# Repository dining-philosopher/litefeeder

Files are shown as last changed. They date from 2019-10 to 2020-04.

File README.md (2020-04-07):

# litefeeder

Semi-automatic passive printable/castable SMD tape feeder for LitePlacer (should work with other pick and place machines with some adjustments).

Watch it in action: https://www.youtube.com/watch?v=S1jxeCK4YC0

Discussion: https://liteplacer.com/phpBB/viewtopic.php?f=11&t=6272 https://groups.google.com/forum/#!topic/openpnp/D-vYZLsAWHc

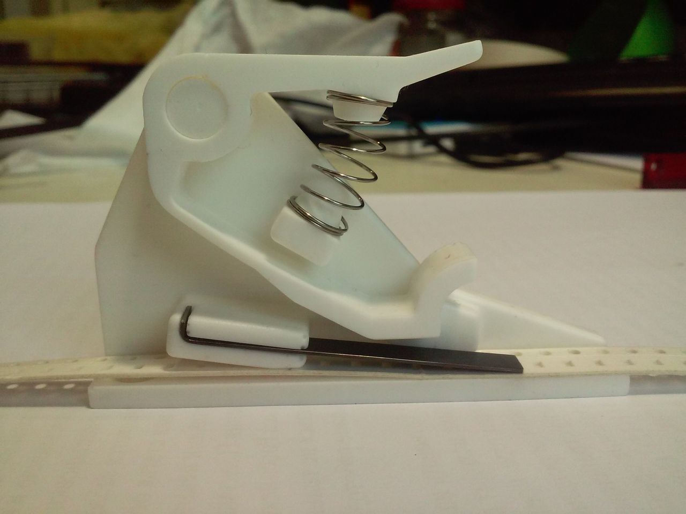
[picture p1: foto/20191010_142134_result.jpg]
assembled feeder


## Update

Jed Smith made film peeler for it, so now it is fully automatic! https://groups.google.com/d/msg/openpnp/D-vYZLsAWHc/gkkAq5XVAgAJ https://loonatec.com/pnp-semi-automatic-feeder/ https://bitbucket.org/Loonatec/pnp_semi-automatic_feeder/ So please use that design until i update this page.

## General notes

The design is inspired by alexavr2's alexfeeder https://github.com/alexavr2/alexfeeder https://alex-avr2.livejournal.com/210450.html and Karl Ekdahl's clockwork feeder https://liteplacer.com/phpBB/viewtopic.php?f=11&t=191 https://vimeo.com/144454867 http://www.knasmusic.com/diyeverything/pickandplace/tapefeeders.php . It is easy to manufacture as the former and requires no additional motion as the latter.

However i think the best cheap feeder design is that found in chinese machines. https://youtu.be/GKw8WOlGR84?t=131 https://youtu.be/y14pdfjYsyo But it requires software support, ~~also i did not find the tape pulling rod assembly sold separately in chinese stores,~~ and i think it should be problematic to attach such assembly to an existing machine. UPD: Here they are: https://www.robotdigg.com/product/1641/Charmhigh-Pull-Pin-Blue-Magnet-Spring-Set-for-36VA-48VA-48VB https://www.robotdigg.com/product/561/Desktop-PnP-Mat https://www.robotdigg.com/product/560/Desktop-PnP-Tape-and-Reel-Receiving-Wheel

### Pros

* No software support required.
* No extra machine head movement required.
* No extra electronics required.
* Easy to manufacture.
* Low cost (about $1 per feeder without labor).

### Cons

* Can only feed 8/4 mm (and maybe 12/4 mm) tape.
* Does not peel the film. You can use 150 - 200 g weights for this or make film peeler as in chinese machines or alexfeeder.

## Manufacturing

### Parts needed

* 0.5*5 mm flat spring. https://www.aliexpress.com/item/32826247091.html
* 0.5\*8\*25 mm coil spring (20 mm may be fine too). https://www.aliexpress.com/item/33054199528.html
* 1.2 mm round nylon line for the tooth (1 mm may be fine too, also you can use metal pins from headers, but it requires additional filing).
* Super glue.
* 7*11 mm nylon spacers for the axle (optional, not needed if you print directly). https://www.aliexpress.com/item/32868508973.html
* Two 2.5*20 mm wood screws.
* One M3*35 screw for machine head.
* One plastic cap for machine head. I use M3 acorn nut https://www.aliexpress.com/item/32963279606.html , but you can use (rounded) M3 long nylon nut https://www.aliexpress.com/item/33002921745.html for better height adjustment or print your own cap.

### [Printing and casting](casting.md)

You can make it with your favorite technology, but if you have no 3d printer at all, or your prints are not strong enough, and/or you prefer casting over 3d printing, you may want to read my [casting description](casting.md).

### Assembly

Drill 1.2 mm hole at about 45° at the end of the dog.
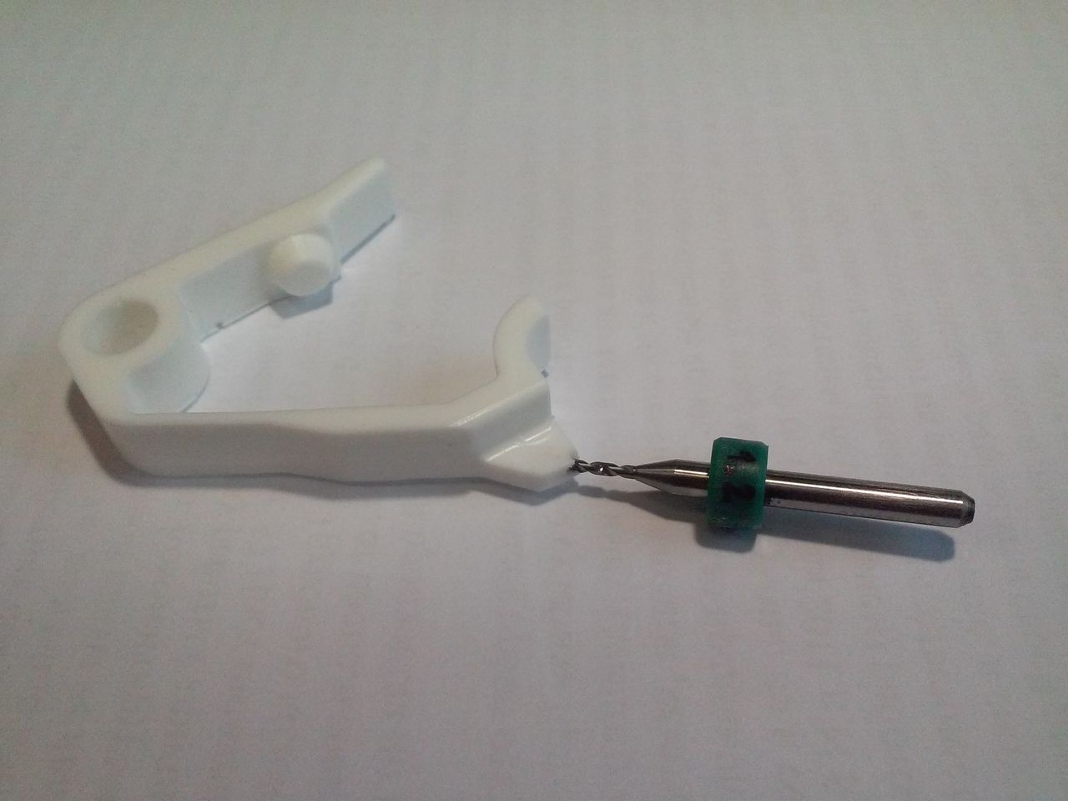
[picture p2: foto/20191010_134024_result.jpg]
drilling tooth hole


Glue 1.2 mm nylon line into this hole.
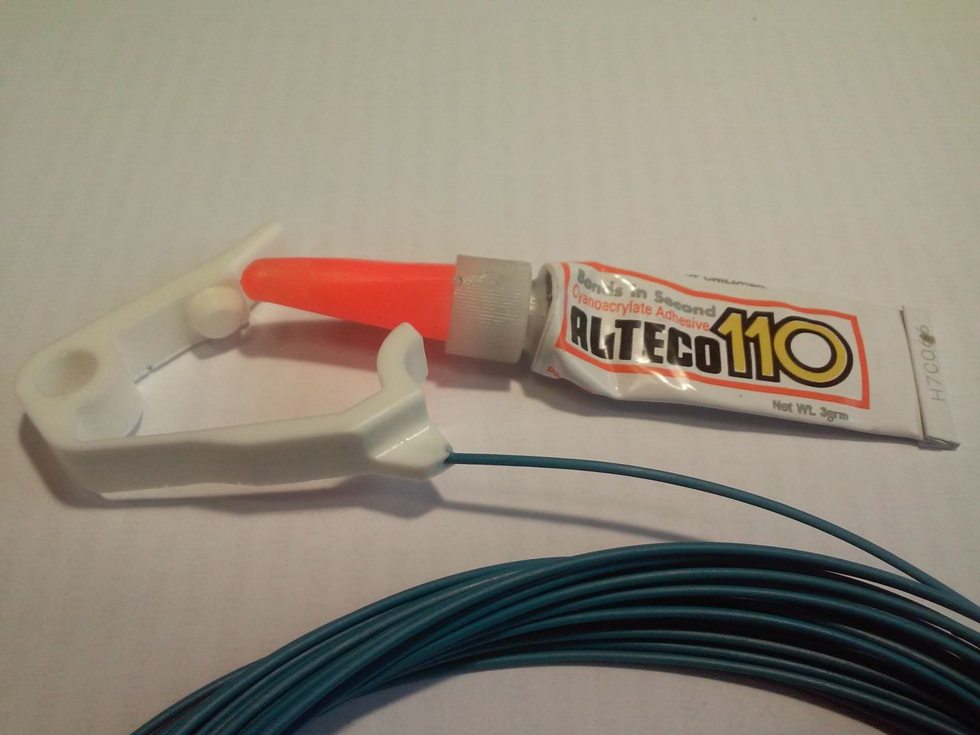
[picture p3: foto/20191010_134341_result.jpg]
gluing nylon tooth

<!---![](foto/20191010_135132_result.jpg "cutting the tooth")-->

Cut the line flush to the vertical face. So we have durable nylon tooth that will push the tape by its holes. You can also use metal pins, nails or whatever you want, but i think nylon line is the easiest way.
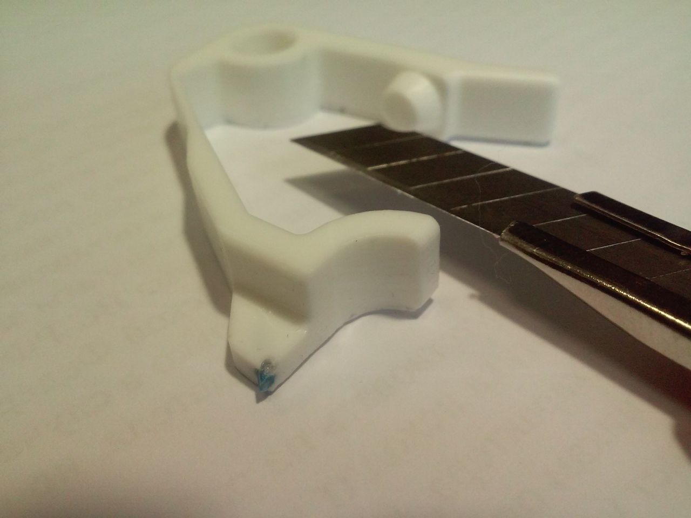
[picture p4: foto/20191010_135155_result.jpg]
cutting the tooth


Bend and cut the flat spring so its long side is 43 - 44 mm and short side is 2 - 3 mm.
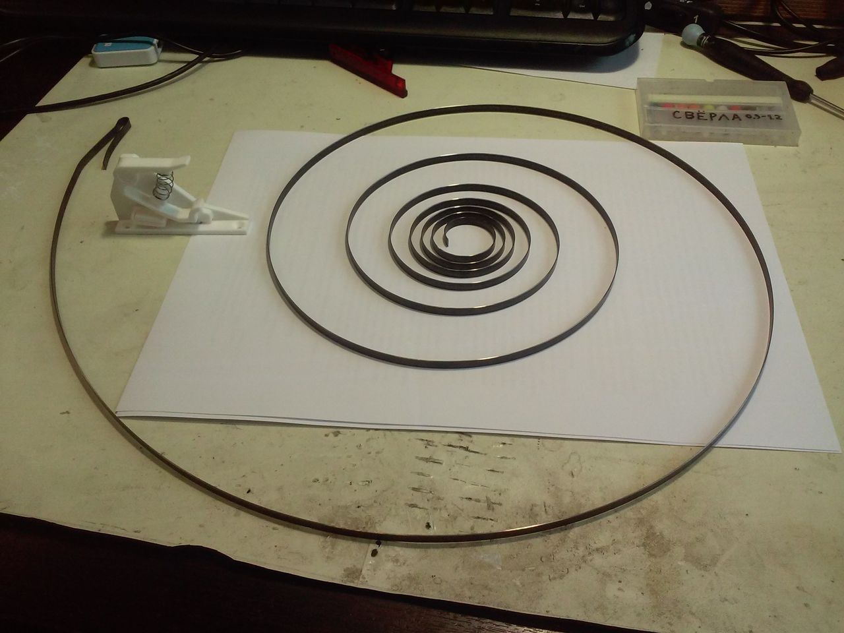
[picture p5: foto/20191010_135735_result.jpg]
flat spring source

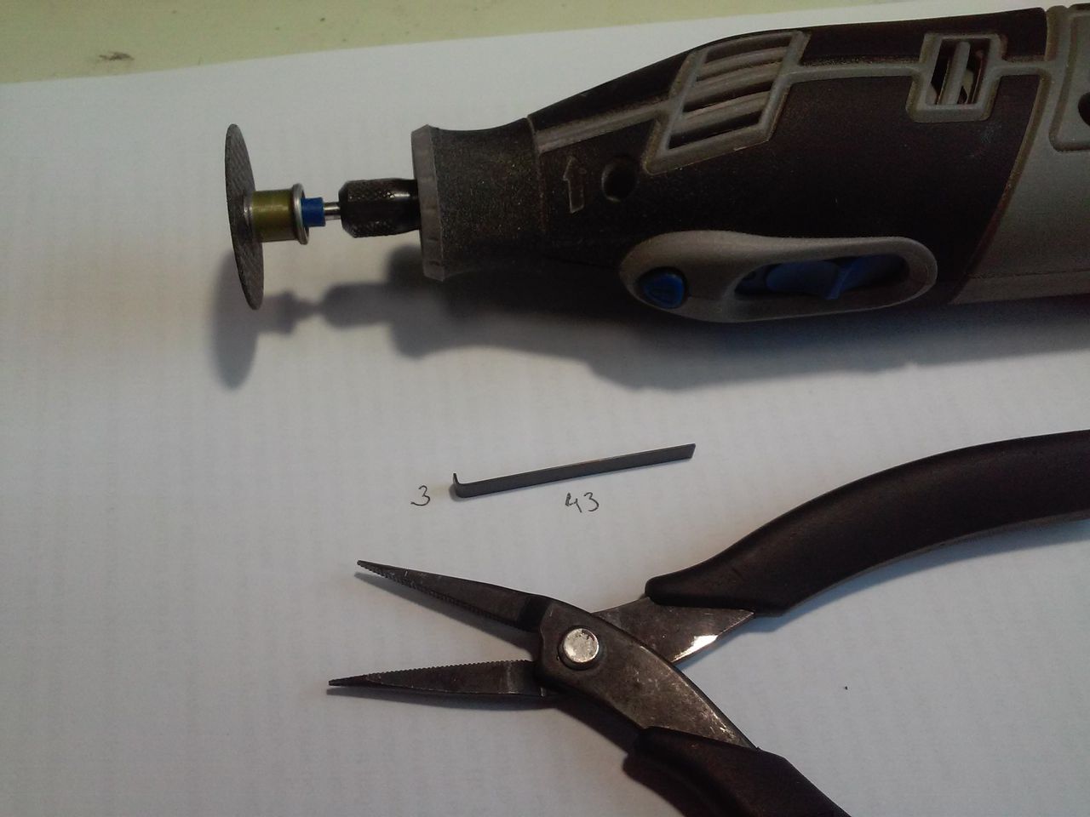
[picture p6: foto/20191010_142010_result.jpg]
cutting flat spring

<!---![](foto/20191010_142122_result.jpg "assembled feeder")-->

Assemble the feeder.
assembled feeder
<!---![](foto/20191010_142910_result.jpg "silicone mold with nylon axle inserted")-->
<!---![](foto/20191010_155337_result.jpg "template aligned to the liteplacer")-->

Replace one of the screws that hold the lower linear bearing with the 35 mm screw and attach the cap nut so your machine can push the lever.
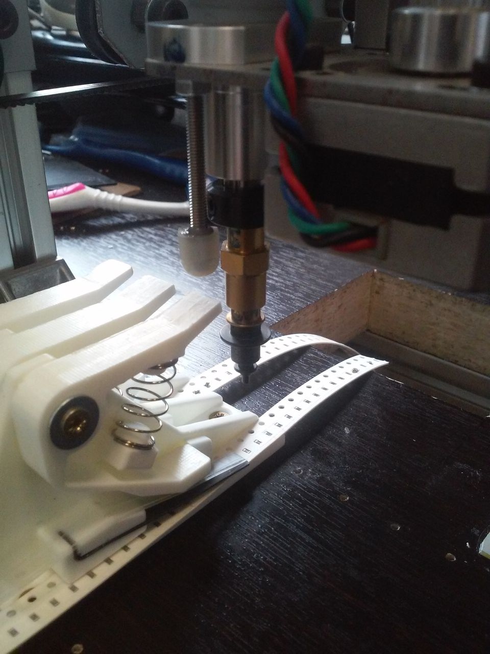
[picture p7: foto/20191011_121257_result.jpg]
feeders in place feeders in place 4


It's time to ruin the table where the machine rests. But before this you need to determine the right Y position for your feeders. Insert some tape into the feeder and push the lever several times. Now you know that it works (hopefully) and the machine nozzle should be above the first part cell not covered by the spring. Try to find such Y position that your feeder pickup coordinate will be almost at the lowest allowed Y coordinate (it is -3 mm in case of the liteplacer, so aim to about -2 mm).
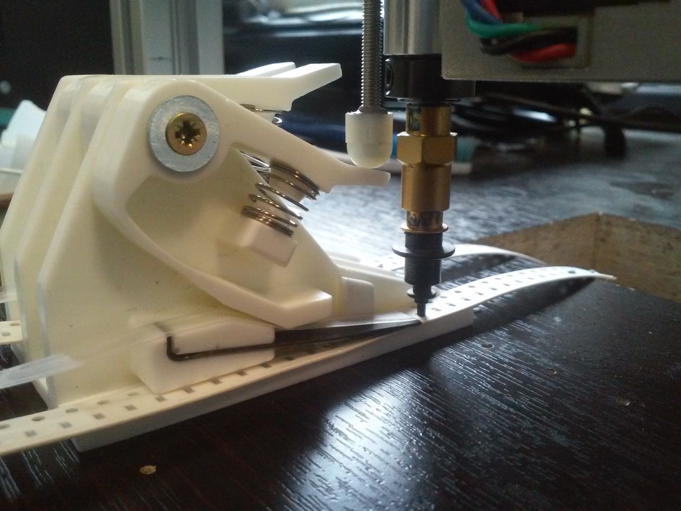
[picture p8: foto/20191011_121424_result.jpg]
feeder in action feeder in action 1

<!---![feeder in action](foto/20191011_121431_result.jpg "feeder in action 2")-->

Print the feeder_screw_template.pdf and stick it to the table (ideally, but not necessary, parallel to the X axis). So your feeders will sit on the table with exactly 12 mm pitch. 
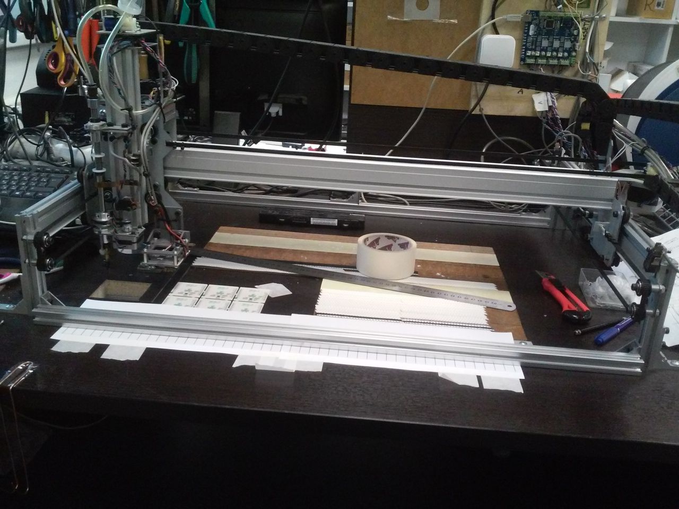
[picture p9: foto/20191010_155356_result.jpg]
template aligned to the liteplacer


Punch holes at the line crossings.
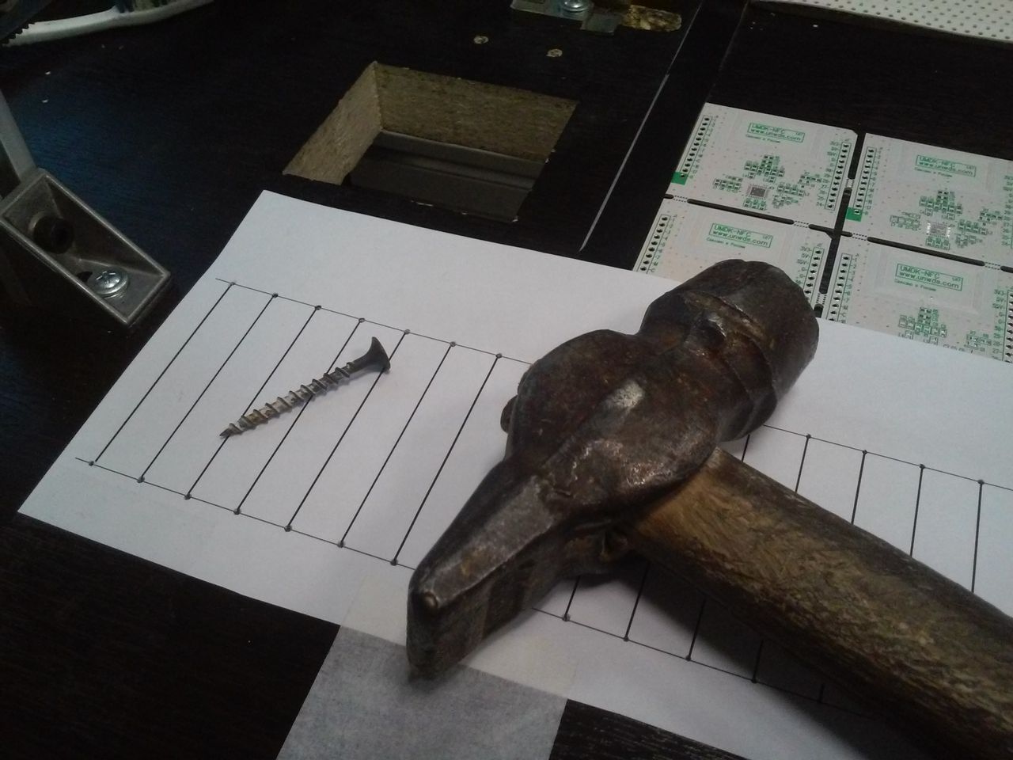
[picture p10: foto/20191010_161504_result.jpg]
punching center holes for the feeders according to the template


Drill 1.5 mm holes.
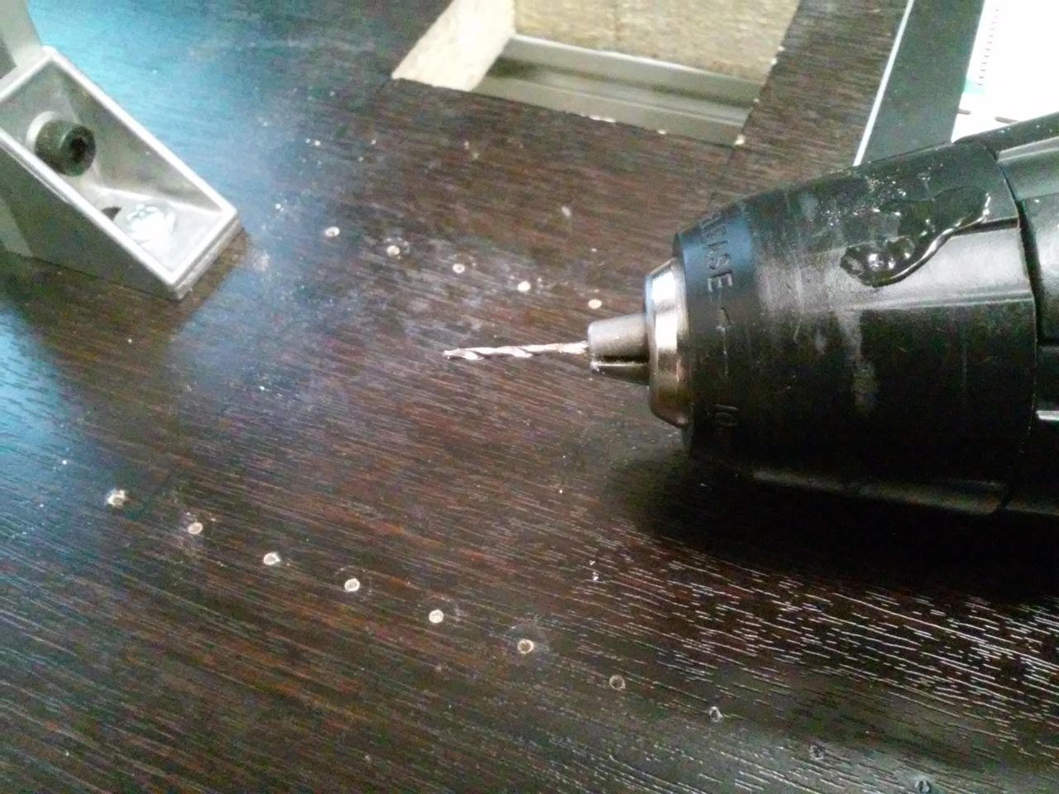
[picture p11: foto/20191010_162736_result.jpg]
drilling holes for the feeders

<!---![feeders in place](foto/20191010_170919_result.jpg "feeders in place 1")-->

Drill 45° 8.5 - 10 mm hole for each feeder into which the used tape will be discarded (not pictured yet). At the first time you may use existing camera hole (the camera is anyway useless with the existing liteplacer software).

Screw some feeders.
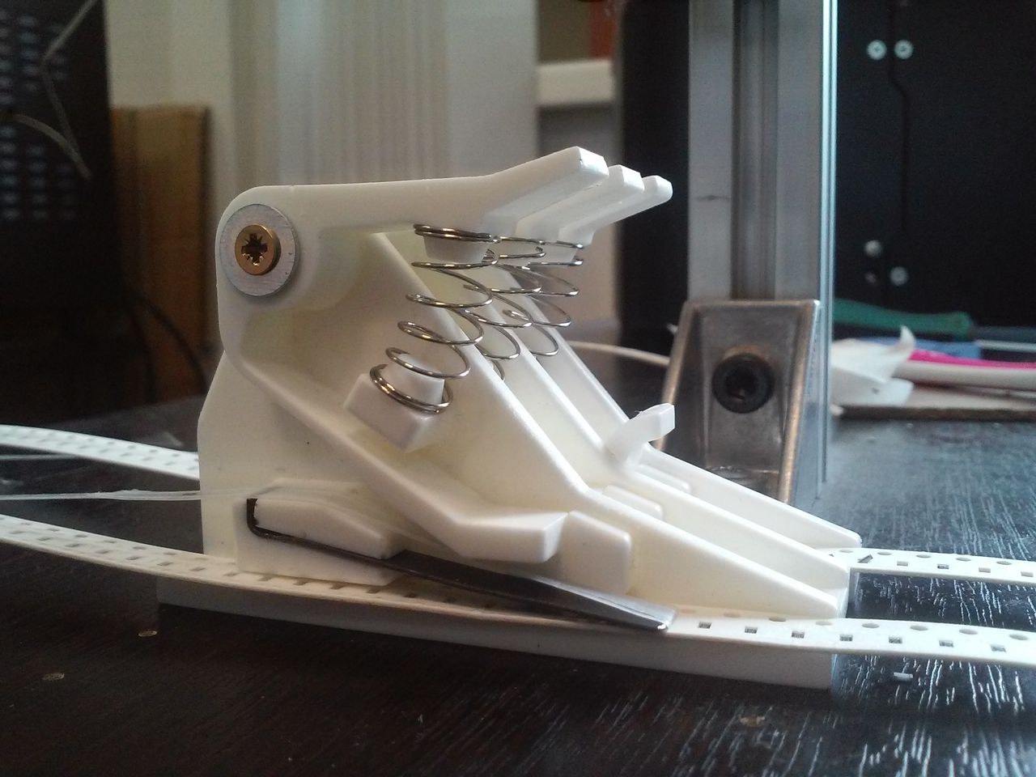
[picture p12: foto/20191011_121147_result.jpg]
feeders in place feeders in place 2

<!---![feeders in place](foto/20191011_121207_result.jpg "feeders in place 3")-->

Invent some reel mount and film peeling mechanism.
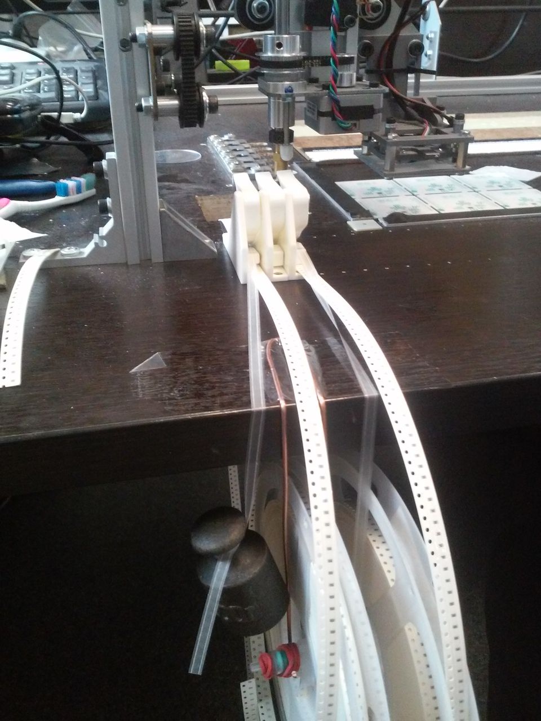
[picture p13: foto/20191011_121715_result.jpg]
reel mount and film peeling mechanism


Profit!

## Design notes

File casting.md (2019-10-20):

# Printing and casting the litefeeder

You can make it with your favorite technology, but bear in mind that it contains plastic spring and rubbing parts, so the plastic should be strong and durable to some extent. For example, UV photopolymers for LCD printers (at least that i have) do not meet this requirements (and also my printer prints quite slowly), so i had to cast my feeders from polyurethane (Smooth-Cast 305).

There are number of polyurethane casting tutorials on youtube, e. g. https://www.youtube.com/watch?v=YGZ2OeQinzw https://www.youtube.com/watch?v=DEVi0mEaJJQ

Platinum silicones are generally better, but they are incompatible with most photopolymers with notable exception of Gorky Liquid Simple https://gorkyliquid.ru/catalog/fotopolimer-dlya-3d-printera/fotopolimernaya_smola_gorky_liquid_simple_krasnaya_1_kg which is quite good by other parameters and also is the cheapest photopolymer in my country. If you can not purchase this resin, try finding another platinum silicone compatible photopolymer or use tin silicone. "Protective coatings" do not work, at least to me.

Release agent is mandatory, especially when pouring second half of the silicone mold over the first half. I use Ease-Release 200. When casting polyurethane, applying release agent before each casting is not necessary, but it is good to apply it every 2 - 3 castings.

Each mold lasts for about 10 - 20 castings (30 if you are lucky, but it slightly grows with each casting).

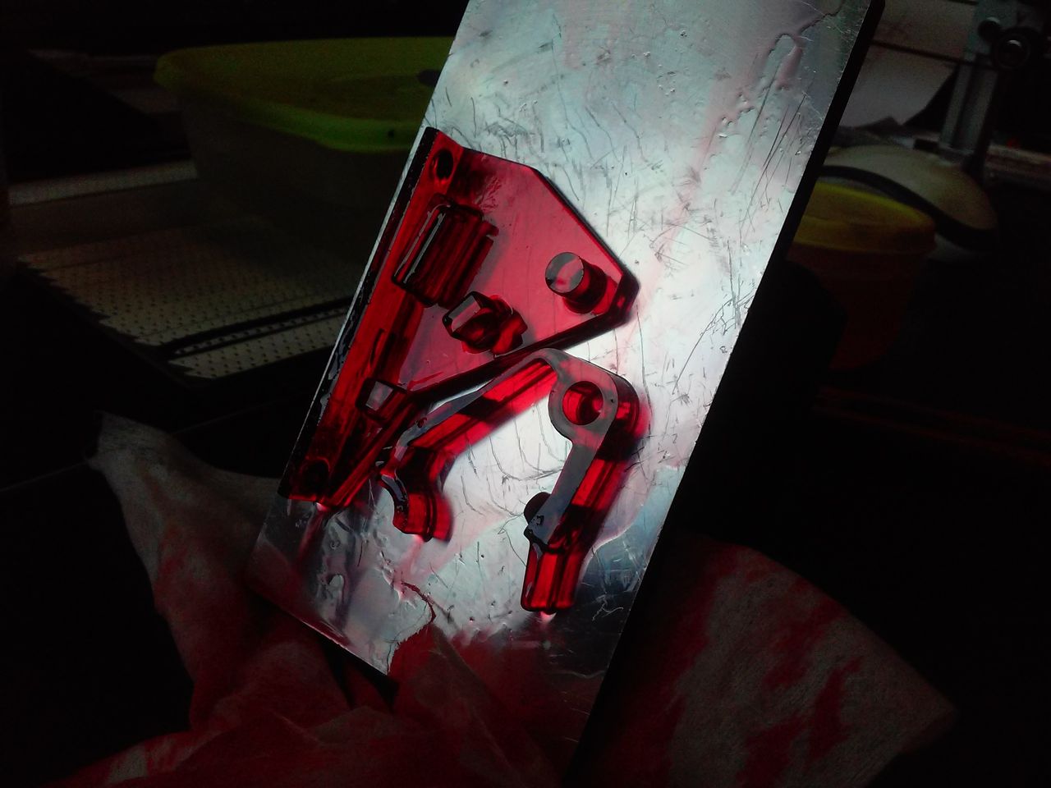
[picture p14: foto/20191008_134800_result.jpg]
printed feeder on the substrate

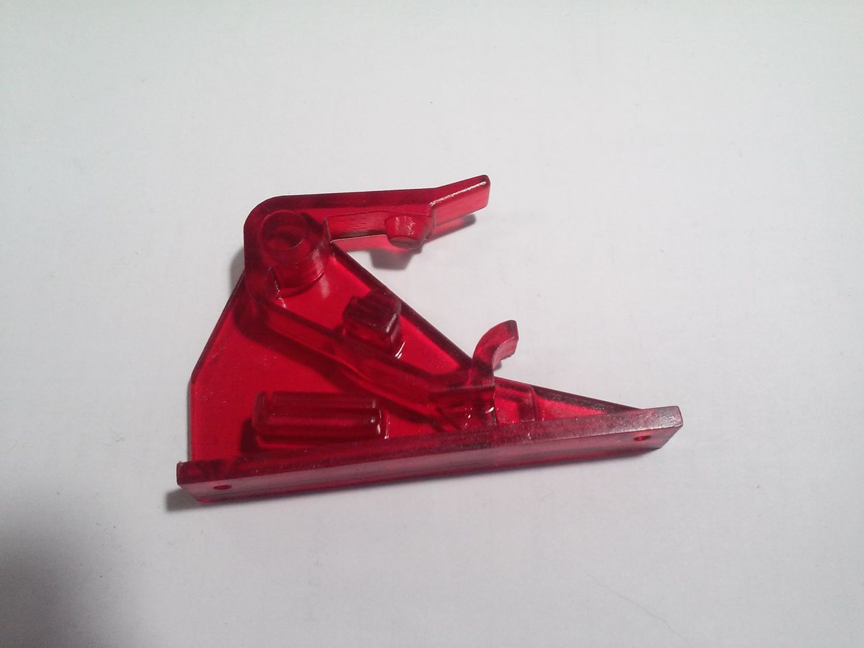
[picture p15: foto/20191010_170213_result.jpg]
printed and washed feeder


Sculpt some keys from modeling clay and glue the feeder parts with the same clay. It is said that some clays are incompatible with platinum silicones, but all my clays work fine.
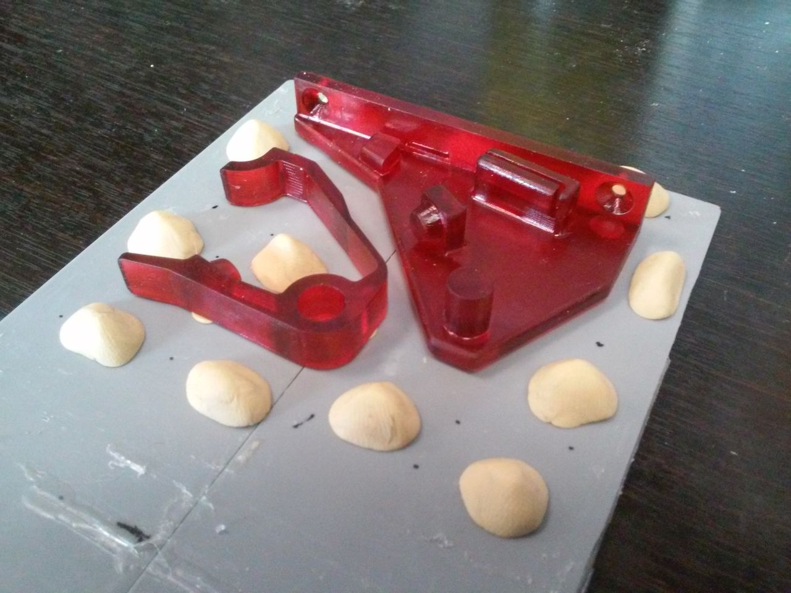
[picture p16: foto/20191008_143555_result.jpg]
preparing for first half silicone molding

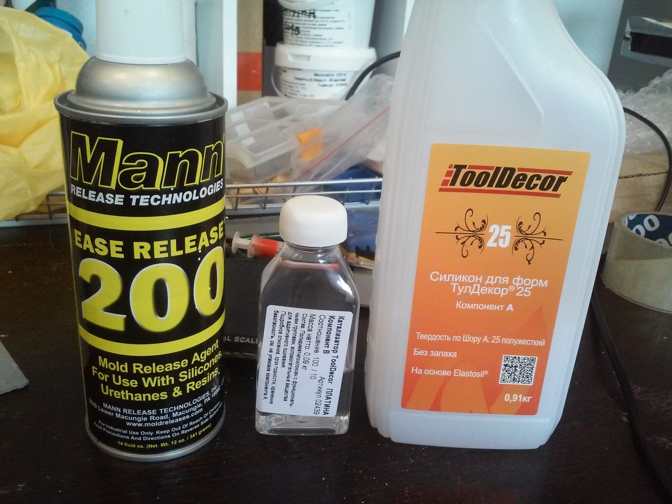
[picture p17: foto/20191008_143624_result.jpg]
silicone and release agent

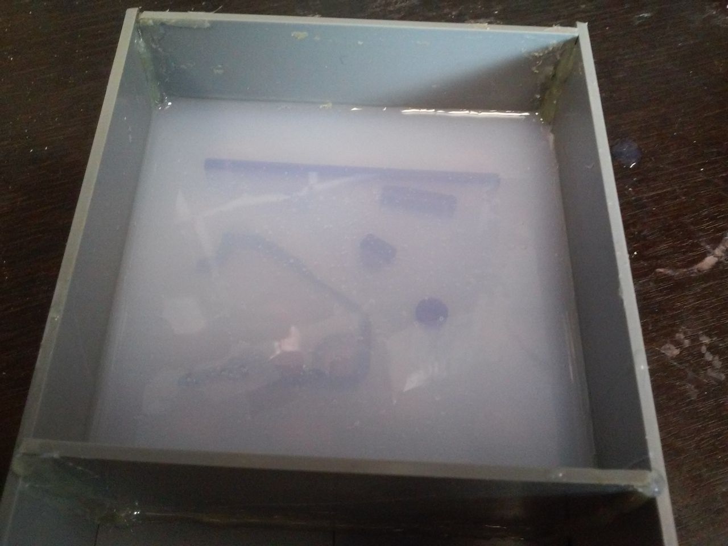
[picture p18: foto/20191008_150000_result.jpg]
first half silicone curing


Remove excess silicone.
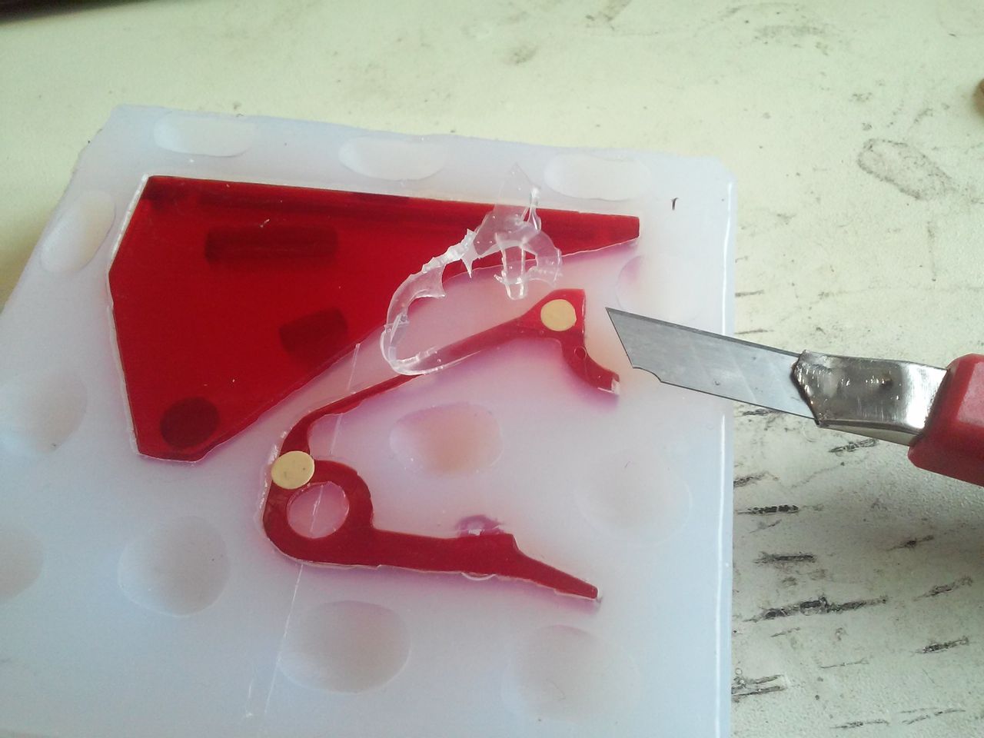
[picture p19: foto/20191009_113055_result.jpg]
removing excess silicone

<!---![](foto/20191009_121346_result.jpg "scotch bucket for second half of the silicone mold")-->

Quick and dirty vessel for the second half. Apply release agent! And do not forget spouts and vents.
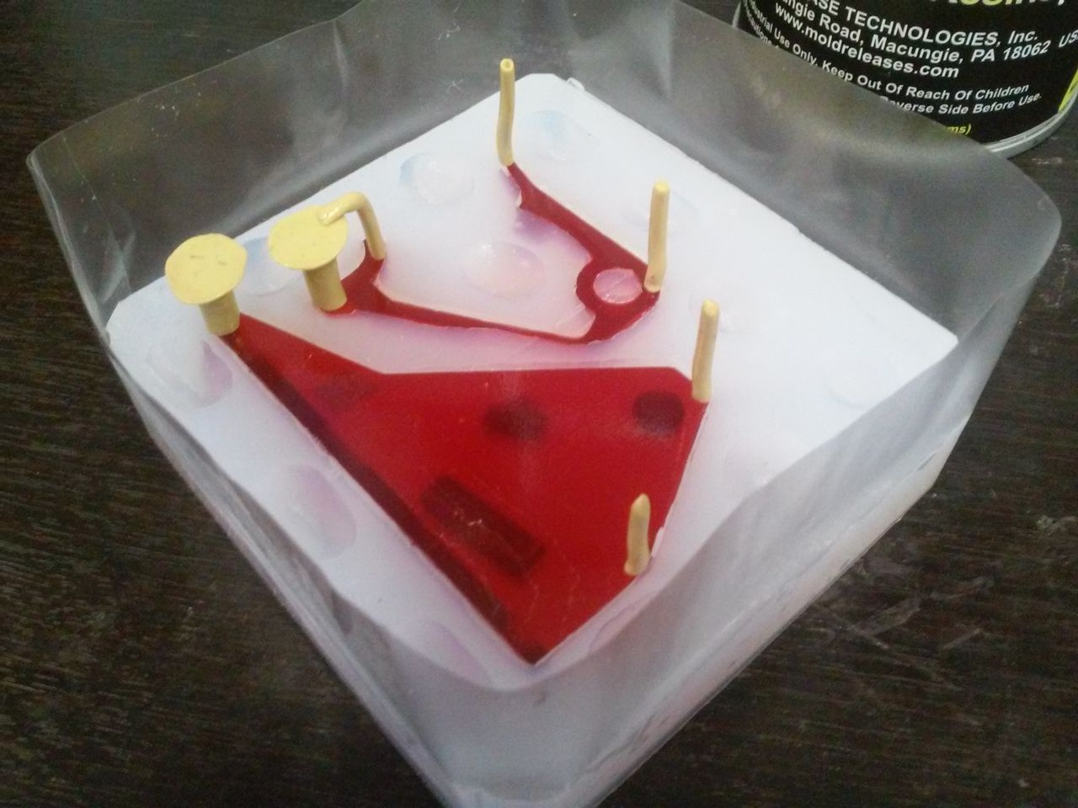
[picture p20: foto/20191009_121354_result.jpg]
scotch bucket for second half of the silicone mold

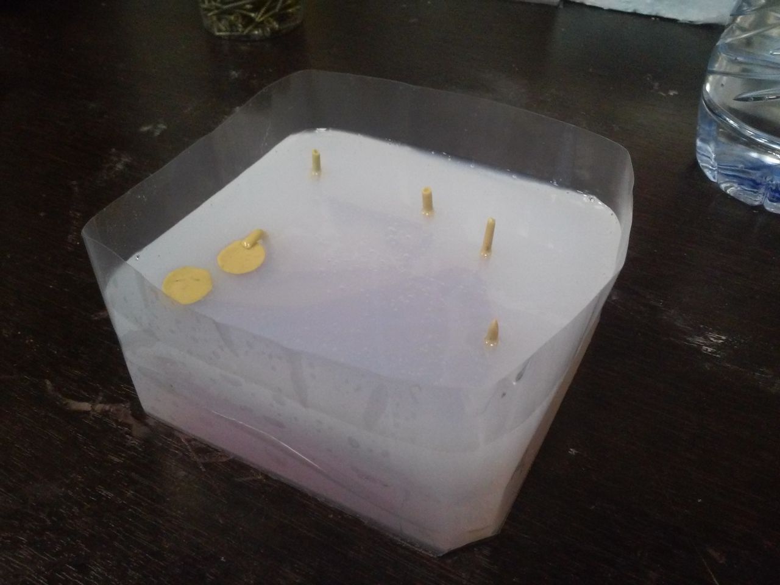
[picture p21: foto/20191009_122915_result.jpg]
scotch bucket for second half of the silicone mold second half silicone curing


Insert nylon axle if you have them (but it also works without it).
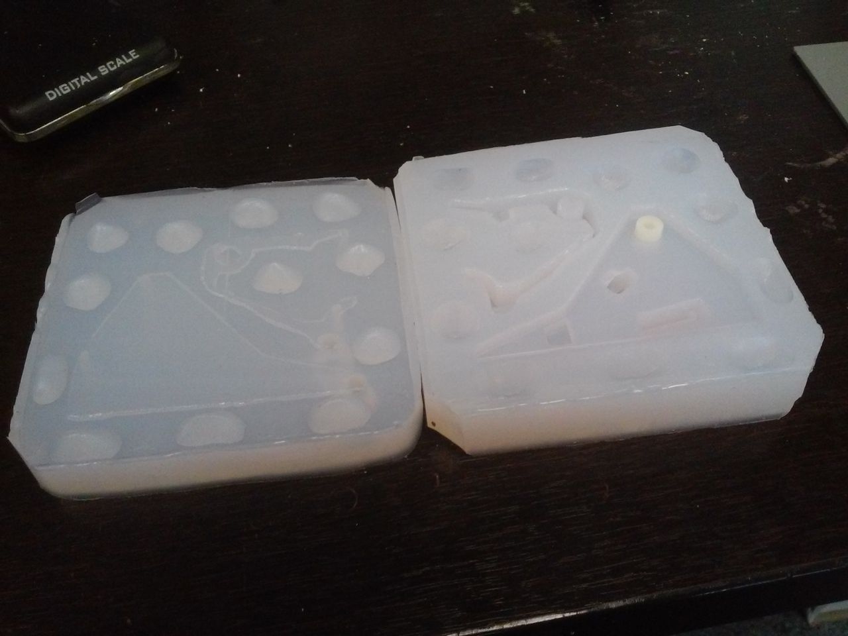
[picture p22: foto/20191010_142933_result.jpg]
silicone mold with nylon axle inserted

<!---![](foto/20191010_143008_result.jpg "silicone mold ready to casting")-->
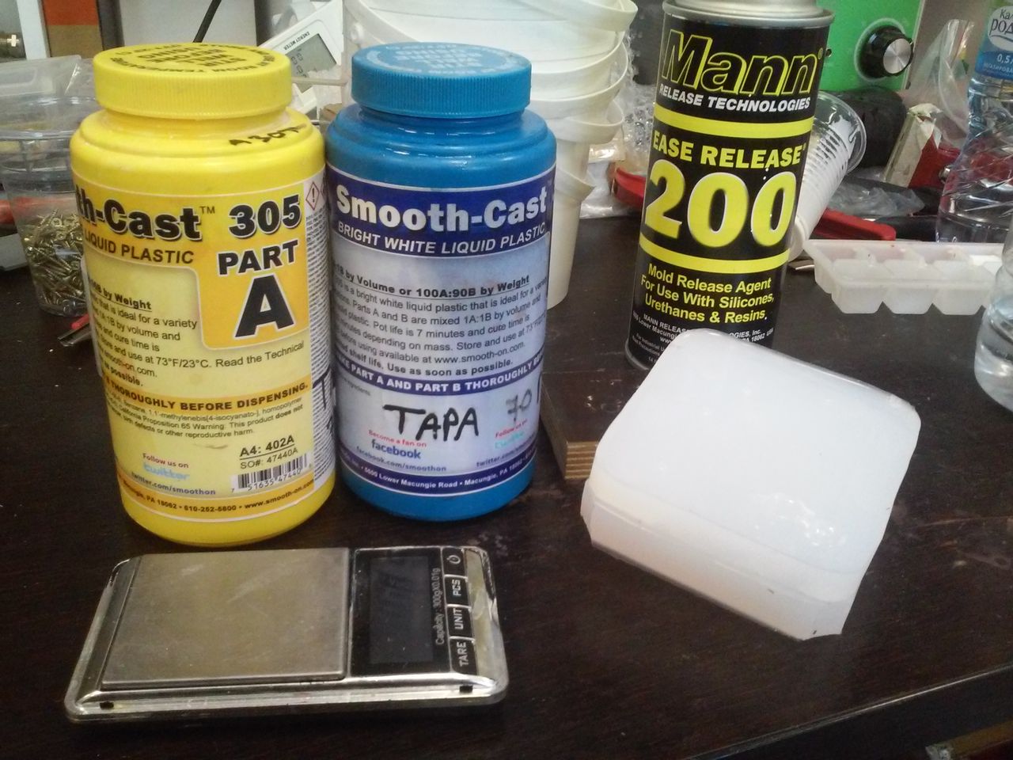
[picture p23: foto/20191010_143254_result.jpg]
silicone mold and polyurethane ready to casting


Extract the casting after about 40 - 50 minutes, remove spouts and vents and wait about 24 hours for polyurethane to fully cure. Or you can bake it in an oven at 60°C for 3 hours as the manual says.

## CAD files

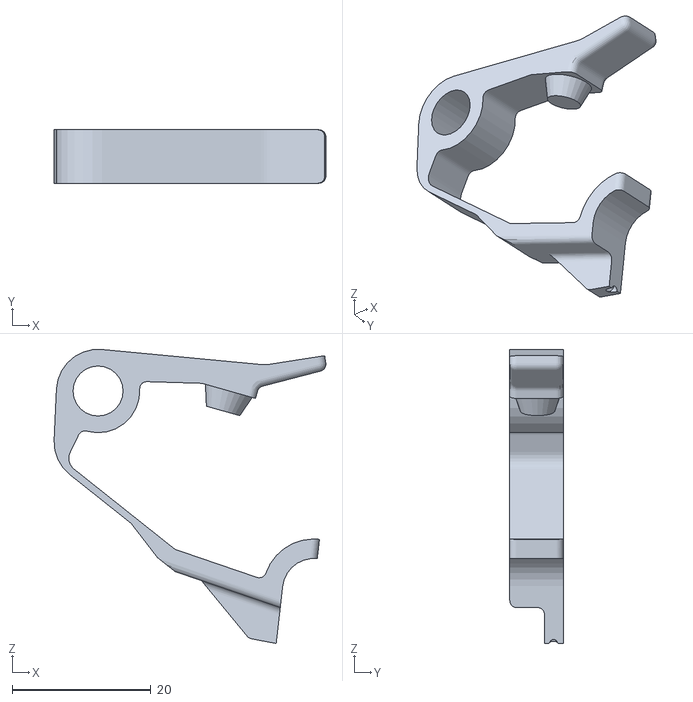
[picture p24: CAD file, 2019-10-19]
feeder40_dog.stl
39.1 x 7.70 x 42.3

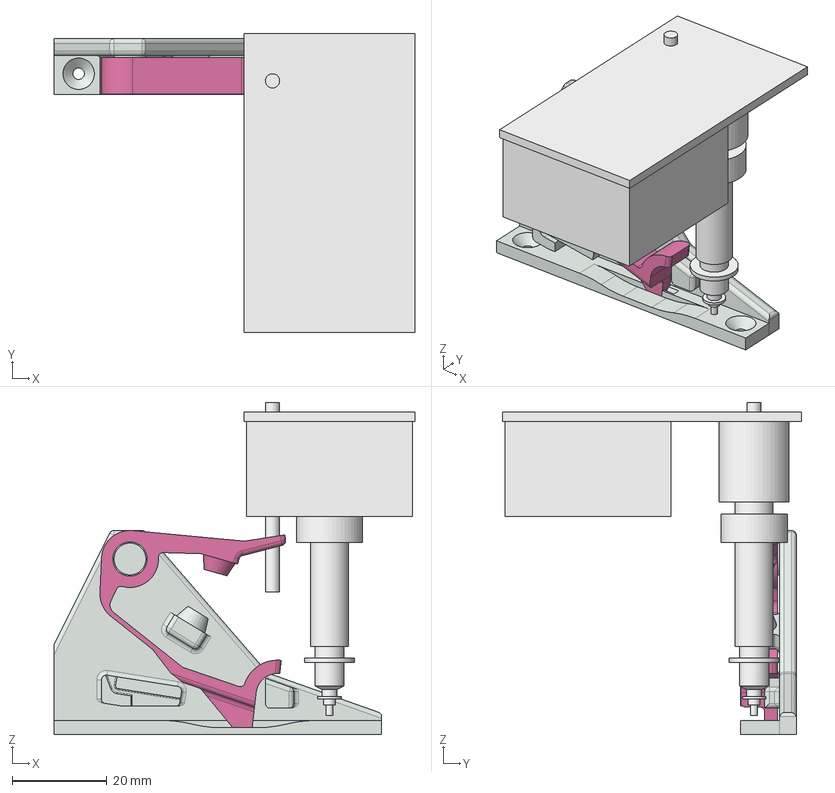
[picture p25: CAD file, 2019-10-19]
feeder40_print.FCStd
76.0 x 63.0 x 70.0 mm
machinehead
dog2

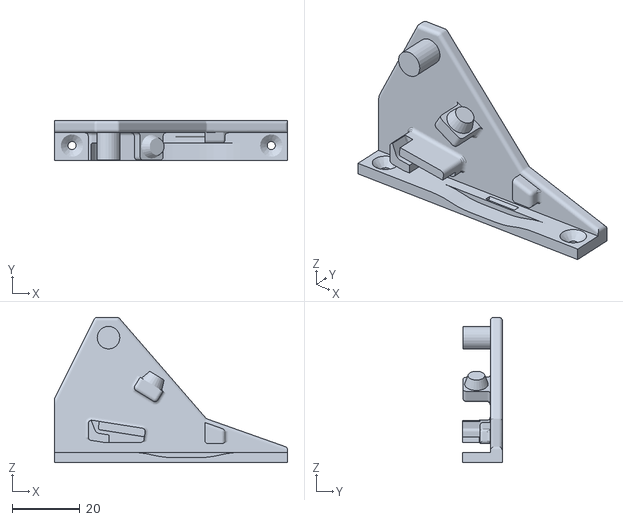
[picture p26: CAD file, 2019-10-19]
feeder40_body.stl
69.0 x 11.8 x 43.0

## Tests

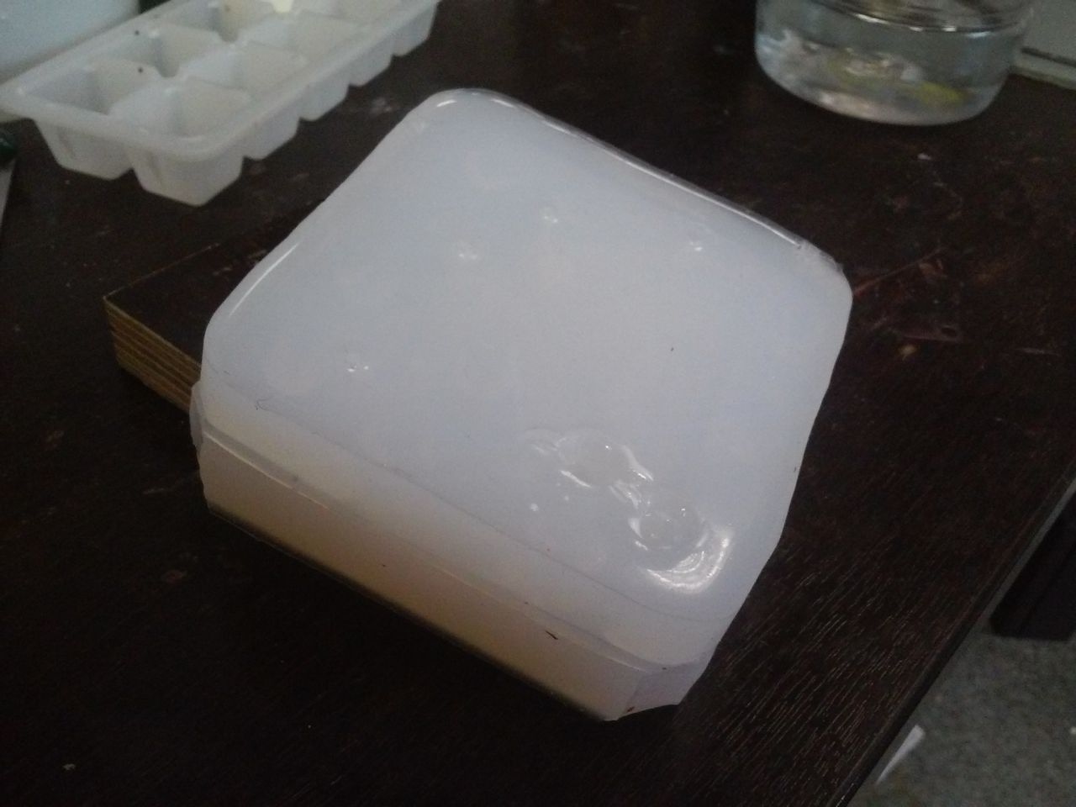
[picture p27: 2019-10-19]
foto/20191010_143008_result.jpg

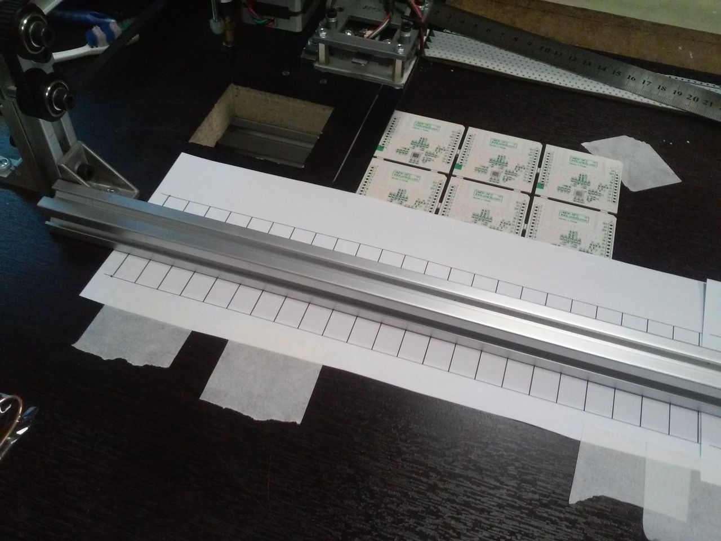
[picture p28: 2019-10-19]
foto/20191010_155337_result.jpg

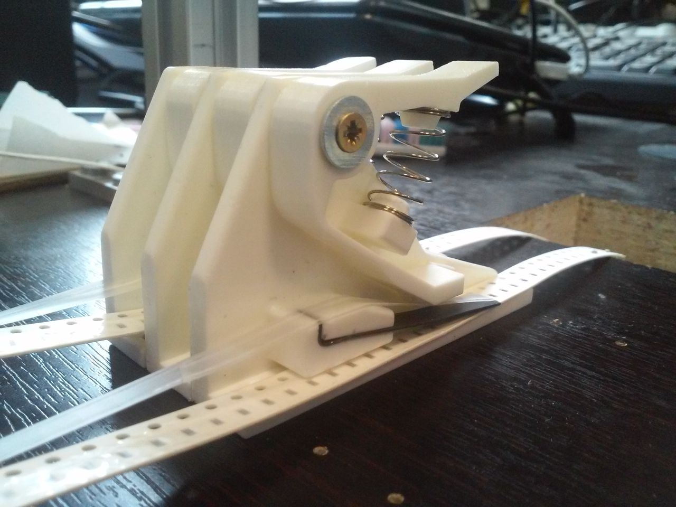
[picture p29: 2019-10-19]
foto/20191011_121207_result.jpg
